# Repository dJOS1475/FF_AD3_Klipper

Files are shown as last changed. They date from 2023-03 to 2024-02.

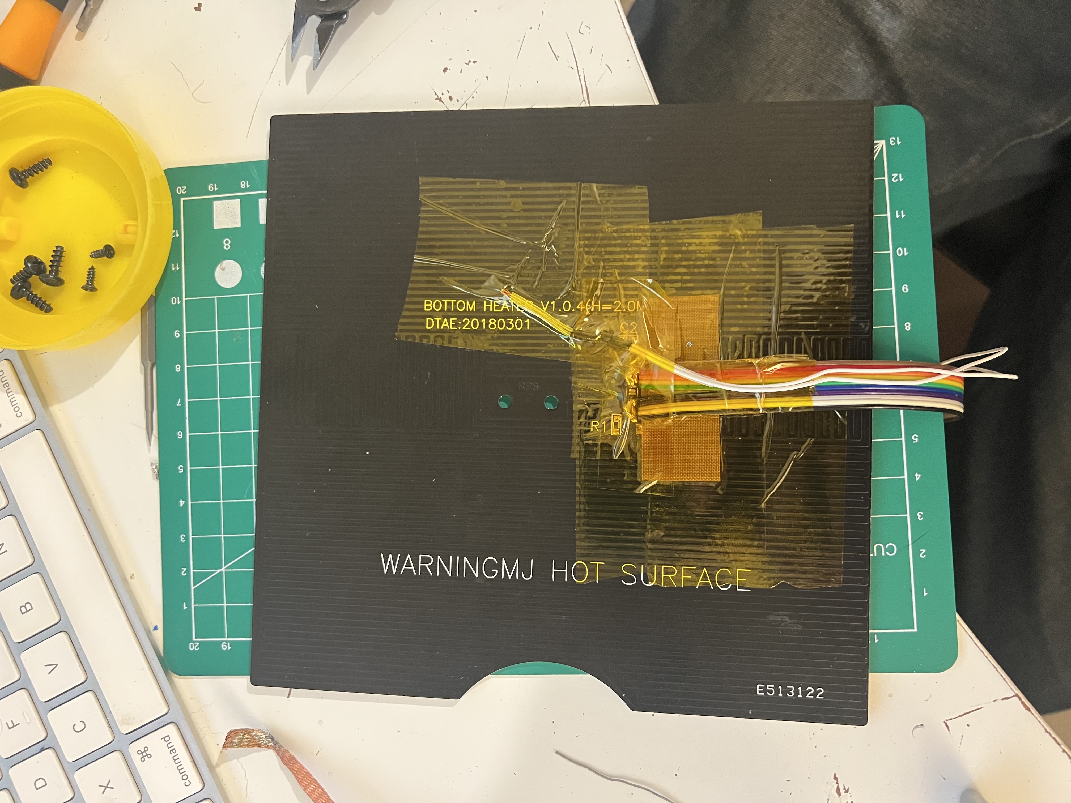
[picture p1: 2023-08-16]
Heater Bed Wiring/IMG_7578.jpeg

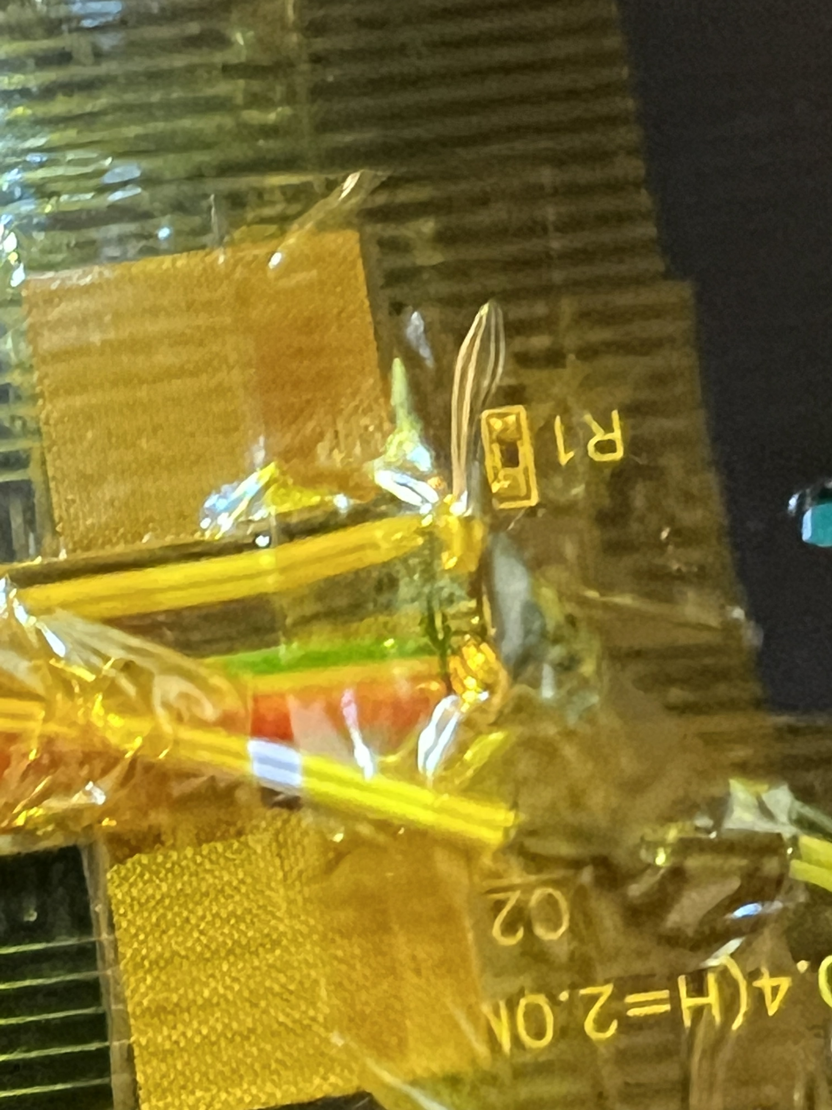
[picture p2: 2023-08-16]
Heater Bed Wiring/IMG_7576.jpeg

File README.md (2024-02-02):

# FlashForge Adventure 3 - Klipper + BTT SKR Mini E3 Upgrade

<p align="center">
  <a>
    Klippventurer logo
  </a>
</p>

Warning: this Upgrade is a Major effort and is recomended for Advanced 3D Printer Users with some electronics skills only. If you would like to keep your OEM mainboard and wiring, please see the Klippventure project by VioSynthax.

# 3D Printed items
are available via Printables:

https://www.printables.com/model/437968-flashforge-adventurer-3-klipper-revo-6-bltouch-btt

# Required Components:
* BigTree Tech SKR Mini E3 v3
* BigTree Tech TFT-35 MZ LCD Screen (with NoTouch E3 Firmware installed)
* PCB's: AD3 HE and AD3 HE BreakOut Boards.
* E3D Revo 6 Hot End
* Good Quality Ribbon cable - ~1.5 meters
* 2x9 Pin IDC Cable Connectors and sockets
* 2x Molex, Micro-Fit 3.0, 43650, 2 Way, 1 Row, Right Angle PCB Headers
* Assorted JST-PH PCB Sockets and Cable Connectors
* 2x PCB Mount Screw Terminal Blocks eg CUI Devices TB004-508-02BE
* 24v to 5v voltage converter eg "1PZ VAC-H15" to power your Raspberry Pi
* Printed Parts

# UPDATES:
* 12th April 2023 - fixed filament macros - please see the Filament_Sensor.cfg file for prerequisites  
* 2nd April 2023 - reduced max speed to 100mm/s - any higher results in layer shifts due to the temps getting too high for the stock stepper motors (at least while printing high tempmaterials like ASA)
* 1st April 2023 - Tweaks to max speed and driver current - the steppers don't seem to like travel speeds over 150mm/s without overheating and causing layer shifts
* 31st March 2023 - Printer now calibrated and Printer.cfg has been updated.
* 30th March 2023 - Everything now works! 

# Videos
FlashForge Adventurer 3 gets a new Brain, Hot-End and Klipper:
https://youtu.be/USZoIhBnA24

Sensorless Homing in Action:
https://youtu.be/0Acrmv7VkdY

and Printing ASA:
https://youtu.be/akCvX6l-e6o

# Klipper Features in use:
* Sensorless Homing
* Adaptive Purge
* Adaptive Mesh Levelling w/ BLTouch
* Auto-Load Filament using Filament Sensor
* Auto Unload Filament when run-out detected
* Unload macro for when you just want to change Filament types/colours etc
* Auto-Extraction Fan at the end of Print (via End G-Code)
* Working LED lighting

# NOTE: 
The factory belt tension on this printer is too loose to exceed 1k acceleration and 100mm/s print speeds. To rectify this you need to retension the X and Y axis belts properly (tight is good, but dont over do it). The Y axis is a PITA as it can only be fixed when the printer is fully disassembled. The Y belt is a continuous loop with no tension adjuster. So you'll need to cut out roughly 5mm from the belt and re-install it as snug as you can get it. I then used some "Selly's Power Grip" to ensure the belts dont jump out of the jaws holding them.

If you still have Y axis layer shifting, I recommend replacing the motor with a better quality unit.

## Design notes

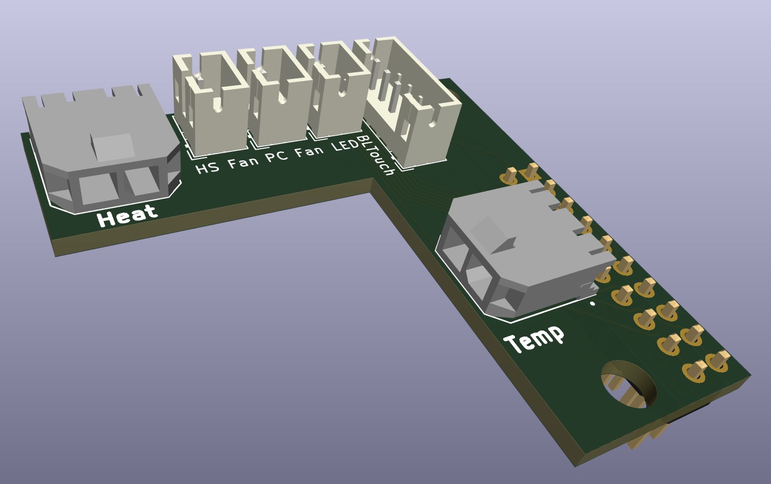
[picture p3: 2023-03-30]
PCB's/Hot End PCB.jpg

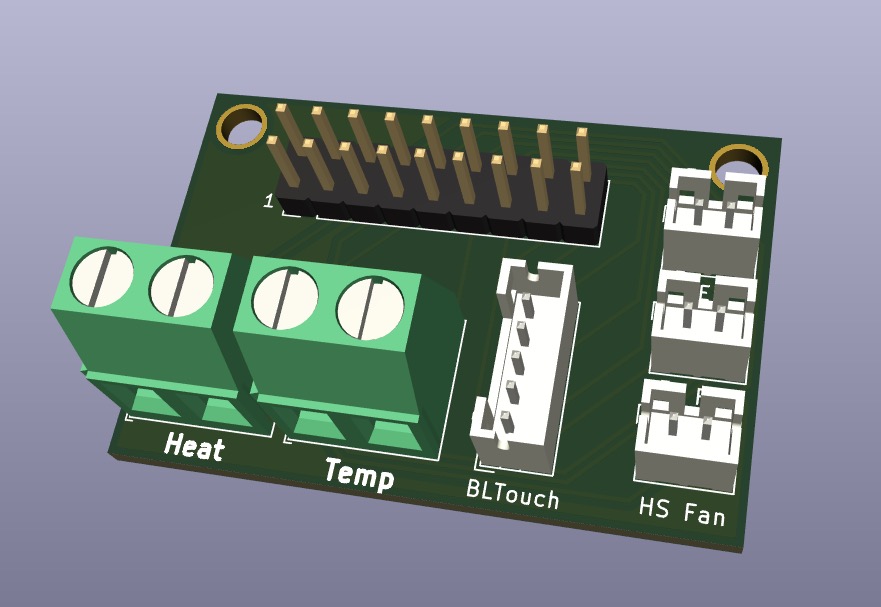
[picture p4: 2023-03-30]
PCB's/Break_Out_Board PCB.jpg

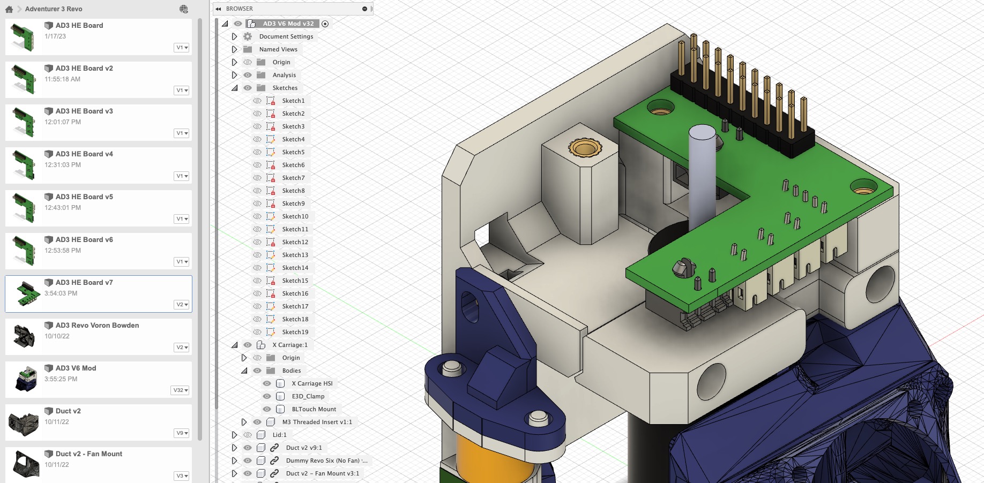
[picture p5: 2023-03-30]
PCB's/Hot End Render.jpg

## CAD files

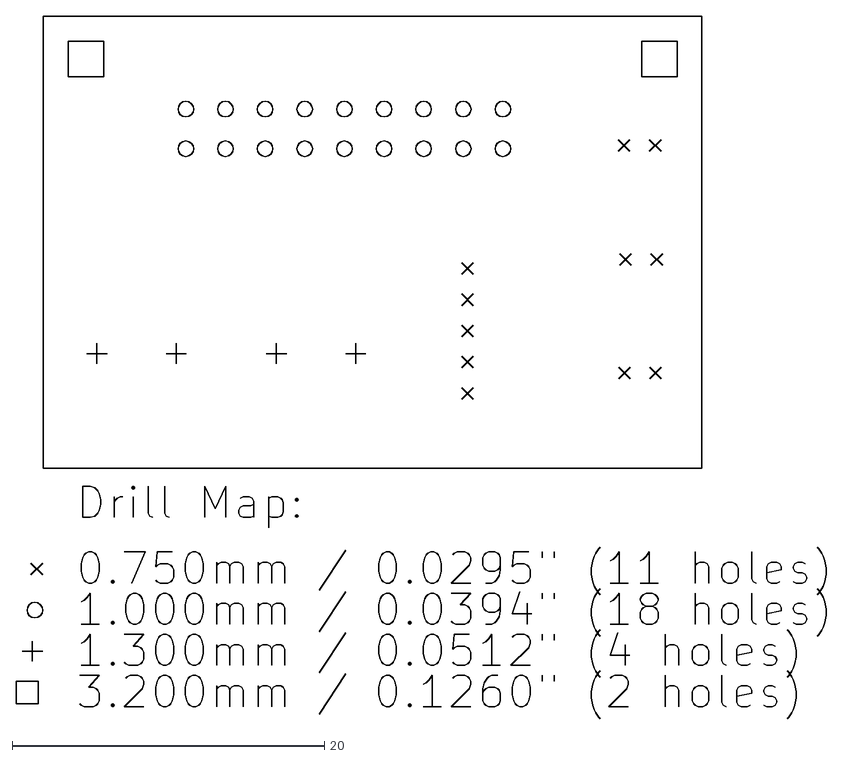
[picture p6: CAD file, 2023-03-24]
PCB's/AD3 Breakout Board/Gerbers/AD3 Breakout Board-drl_map.dxf
51.9 x 45.0

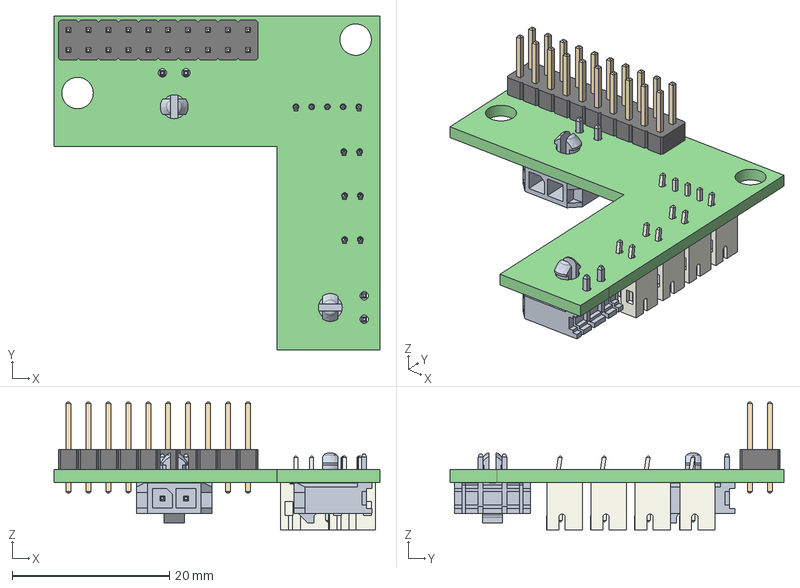
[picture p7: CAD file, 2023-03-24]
PCB's/AD3 HE Board/AD3 HE Board.step
41.5 x 42.5 x 16.2 mm
AD3 HE Board PCB

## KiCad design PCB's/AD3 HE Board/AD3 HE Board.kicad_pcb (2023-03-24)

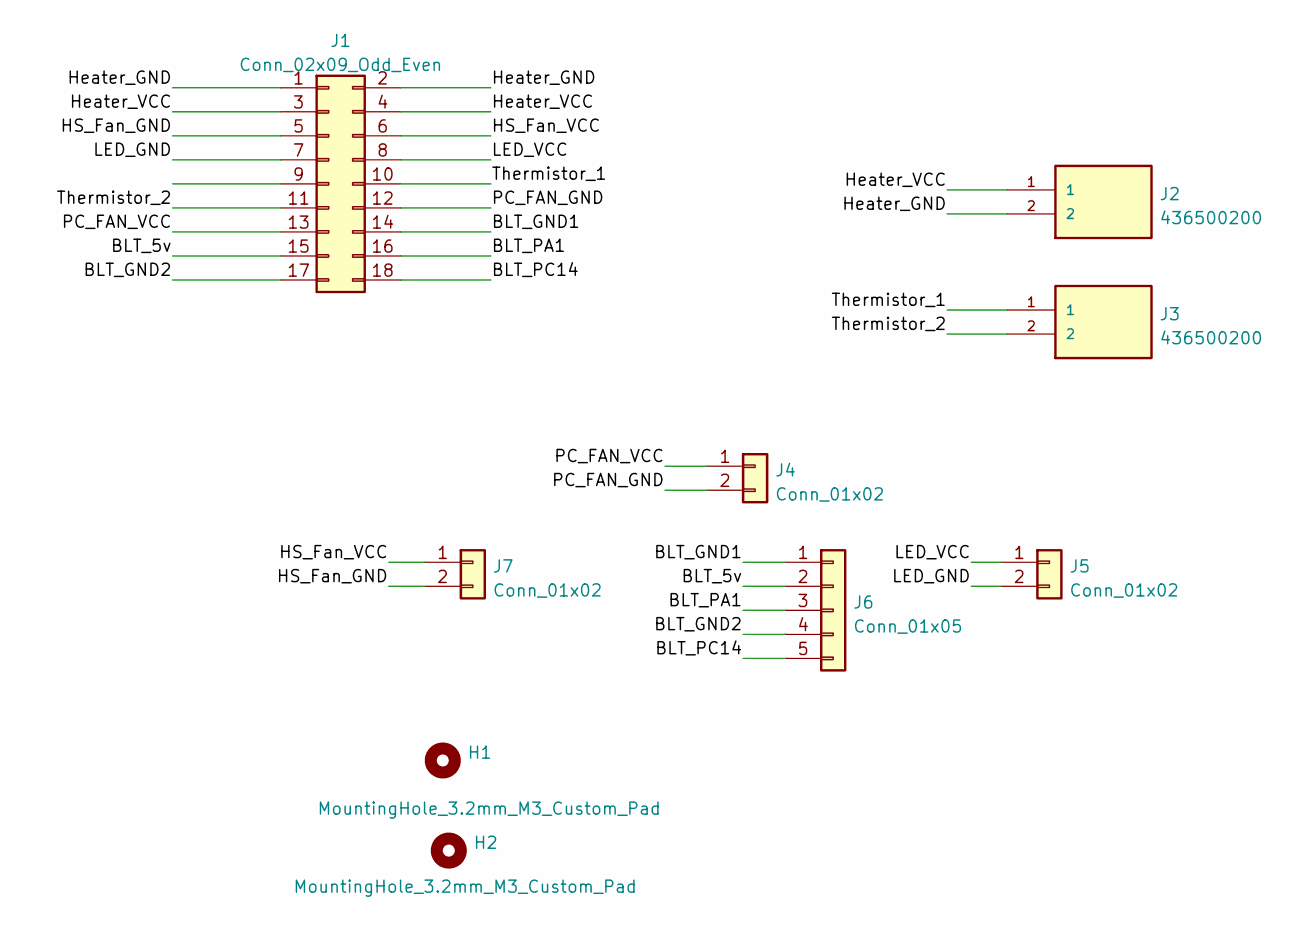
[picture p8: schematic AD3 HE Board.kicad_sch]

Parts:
H1, H2: MountingHole_3.2mm_M3_Custom_Pad
J1: Conn_02x09_Odd_Even; PinHeader_2x09_P2.54mm_Vertical
J2, J3: 436500200; MOLEX_436500200; PARTREV D7
J4, J5, J7: Conn_01x02; JST_PH_B2B-PH-K_1x02_P2.00mm_Vertical
J6: Conn_01x05; JST_PH_B5B-PH-K_1x05_P2.00mm_Vertical

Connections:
/BLT_5v: J1.15, J6.2
/BLT_GND1: J1.14, J6.1
/BLT_GND2: J1.17, J6.4
/BLT_PA1: J1.16, J6.3
/BLT_PC14: J1.18, J6.5
/HS_Fan_GND: J1.5, J7.2
/HS_Fan_VCC: J1.6, J7.1
/Heater_GND: J1.1, J1.2, J2.2
/Heater_VCC: J1.3, J1.4, J2.1
/LED_GND: J1.7, J5.2
/LED_VCC: J1.8, J5.1
/PC_FAN_GND: J1.12, J4.2
/PC_FAN_VCC: J1.13, J4.1
/Thermistor_1: J1.10, J3.1
/Thermistor_2: J1.11, J3.2

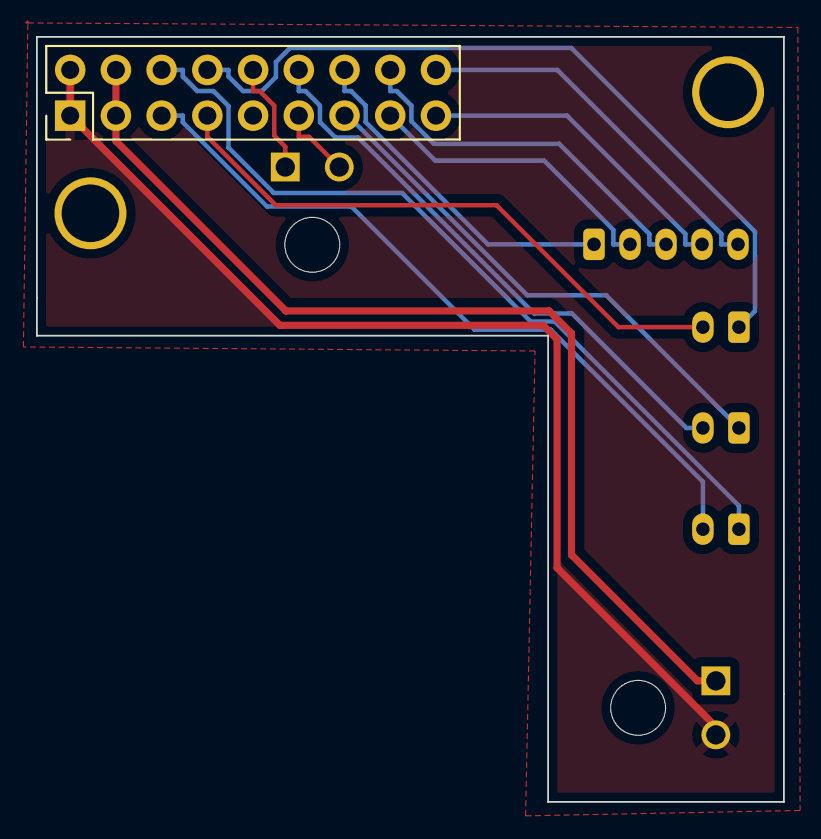
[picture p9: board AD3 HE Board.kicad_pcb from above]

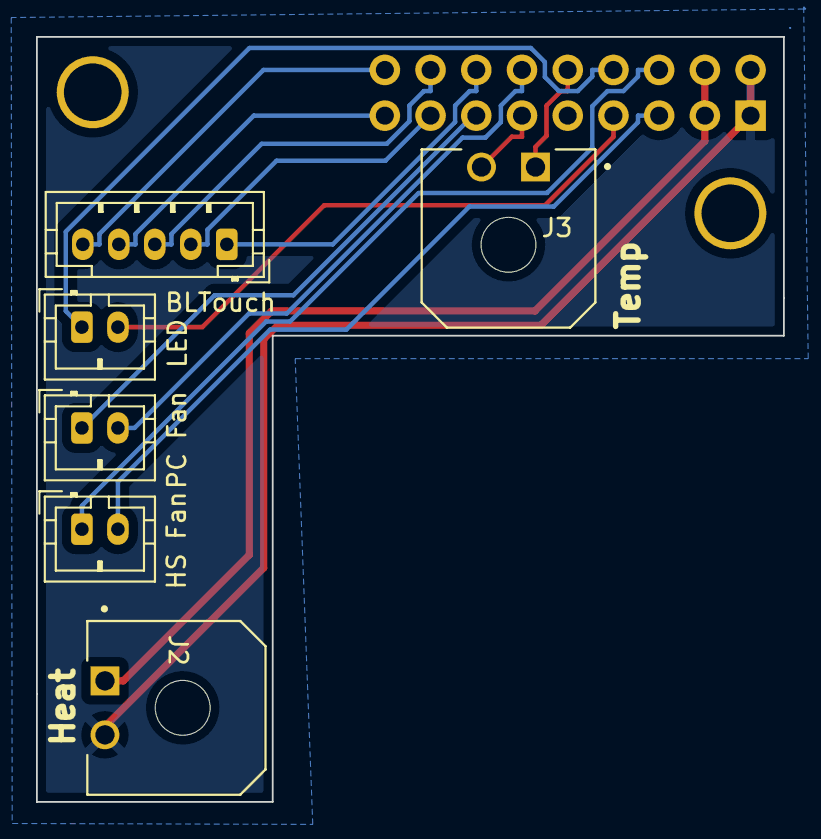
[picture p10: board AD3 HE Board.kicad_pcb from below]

Board: 2 copper layers, 41.5 x 42.5 mm, 9 parts (6 on the bottom side), 15 nets.

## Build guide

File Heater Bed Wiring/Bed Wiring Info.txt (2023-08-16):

Basically you dont want to use the inner 2 traces as that is the old Thermistor. 
I couldnt work out a way to make it reliable, so I replaced it with a normal glass bead thermistor and removed the SMD components from it.

The rest of the pads are split evenly on either side as the heater power. 
It's not important which way you wire it as it isnt polarised.

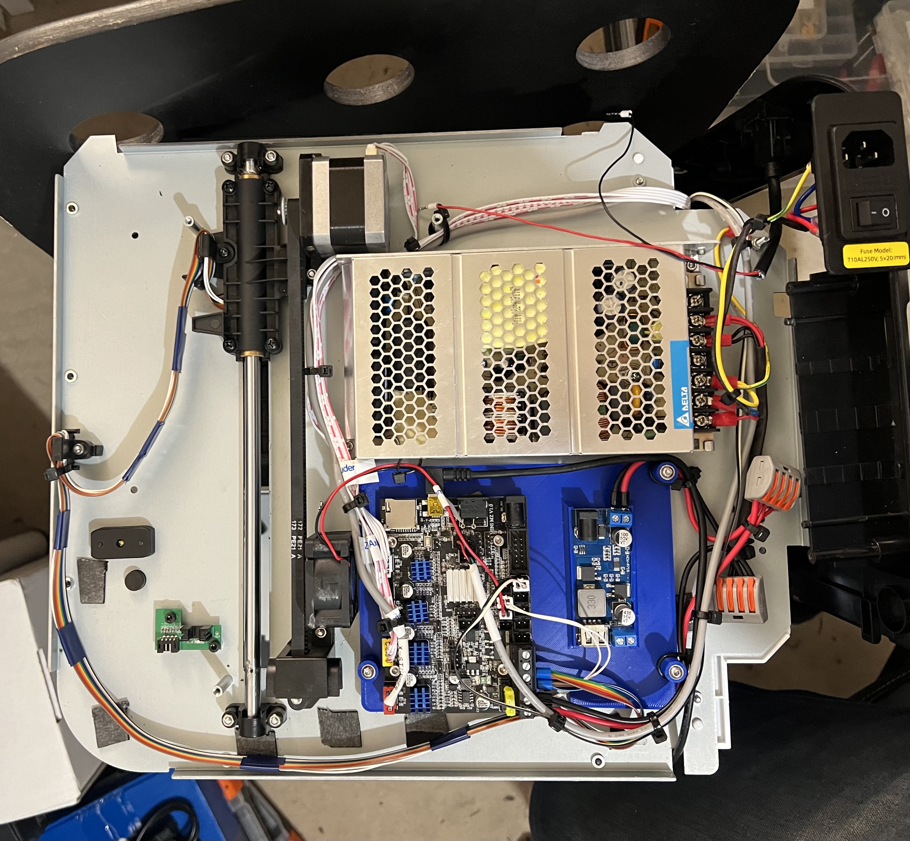
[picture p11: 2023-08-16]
Heater Bed Wiring/IMG_7589.jpeg

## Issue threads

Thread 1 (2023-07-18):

X should be Y

devimauz, 2023-07-18:
https://github.com/dJOS1475/FF_AD3_Klipper/blame/f0657e87483728f9c68891eaef96df8fc055af23/Klipper%20Base%20Config/macros.cfg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

dJOS1475, 2023-07-19:
Could catch, I've fixed it.

dJOS1475, 2023-07-19:
fixed

Closed 2023-07-19.

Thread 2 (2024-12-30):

Different versions of the heated bed

tweinschenk, 2024-12-30:
Hello,

I read the bed wiring info and while looking at my own bed I have to say that the outer two traces are connected to the original thermistor. Maybe we have different versions of the bed? But they even have the same version number: V1.0.4

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

Maybe you can confirm that yours is different and add a note that there are different versions :)

dJOS1475, 2024-12-30:
Howdy, even tho they say they are the same version, your text is in a different orientation to mine. If you rotated your board to the same as shown in my pics, your text would be upside down.

dJOS1475, 2024-12-30:
Ps R1 is a resistor, not the thermistor - it just there as an initial load for the original electronics.

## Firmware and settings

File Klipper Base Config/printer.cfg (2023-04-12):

# This file contains common pin mappings for the BIGTREETECH SKR mini
# E3 v3.0. To use this config, the firmware should be compiled for the
# STM32G0B1 with a "8KiB bootloader" and USB communication.

# The "make flash" command does not work on the SKR mini E3. Instead,
# after running "make", copy the generated "out/klipper.bin" file to a
# file named "firmware.bin" on an SD card and then restart the SKR
# mini E3 with that SD card.

# See docs/Config_Reference.md for a description of parameters.

[include Adaptive_Mesh.cfg]
[include Adaptive_Purge.cfg]
[include macros.cfg] 
[include probe_bltouch.cfg]
[include mainsail.cfg]
[include Filament_Sensor.cfg]

[printer]
kinematics: cartesian
max_velocity: 150
max_accel: 3000
max_accel_to_decel: 3000
max_z_accel: 25
square_corner_velocity: 5

[stepper_x]
step_pin: PB13
dir_pin: PB12
enable_pin: !PB14
microsteps: 16
rotation_distance: 33.36
endstop_pin: tmc2209_stepper_x:virtual_endstop
homing_retract_dist: 0
homing_speed: 25
position_endstop: 0
position_max: 156


[tmc2209 stepper_x]
uart_pin: PC11
tx_pin: PC10
uart_address: 0
run_current: 0.800
stealthchop_threshold: 999999
diag_pin: ^PC0      # Set to MCU pin connected to TMC DIAG pin
driver_SGTHRS: 75  # 255 is most sensitive value, 0 is least sensitive


[stepper_y]
step_pin: PB10
dir_pin: PB2
enable_pin: !PB11
microsteps: 16
rotation_distance: 33.38
endstop_pin: tmc2209_stepper_y:virtual_endstop
homing_retract_dist: 0
homing_speed: 25
position_endstop: 0
position_max: 148


[tmc2209 stepper_y]
uart_pin: PC11
tx_pin: PC10
uart_address: 2
run_current: 0.800
stealthchop_threshold: 999999
diag_pin: ^PC1      # Set to MCU pin connected to TMC DIAG pin
driver_SGTHRS: 75  # 255 is most sensitive value, 0 is least sensitive


[stepper_z]
step_pin: PB0
dir_pin: PC5
enable_pin: !PB1
microsteps: 16
rotation_distance: 6.25
# endstop_pin: PC2
endstop_pin: probe:z_virtual_endstop
# position_endstop: 0
position_max: 150
homing_speed: 20
second_homing_speed: 15
homing_retract_dist: 5

[tmc2209 stepper_z]
uart_pin: PC11
tx_pin: PC10
uart_address: 1
run_current: 0.800
stealthchop_threshold: 999999


[extruder]
step_pin: PB3
dir_pin: !PB4
enable_pin: !PD1
microsteps: 16
rotation_distance: 31
nozzle_diameter: 0.4
filament_diameter: 1.750
heater_pin: PC8
sensor_type: ATC Semitec 104NT-4-R025H42G 
sensor_pin: PC4
min_temp: 0
max_temp: 300
min_extrude_temp: 180
max_extrude_only_distance: 900
max_extrude_only_velocity: 120
max_extrude_only_accel: 1000
min_extrude_temp: 180
max_extrude_cross_section: 5
pressure_advance: 0.050
# pressure_advance_smooth_time: 0.04

[tmc2209 extruder]
uart_pin: PC11
tx_pin: PC10
interpolate: True
uart_address: 3
run_current: 1.3
stealthchop_threshold: 0


[heater_bed]
heater_pin: PC9
sensor_type: Generic 3950
sensor_pin: PA0
min_temp: 0
max_temp: 120


[idle_timeout]
gcode:
  PANEL_BEEP   
  M84 ; disable motors
  TURN_OFF_HEATERS
  SET_PIN PIN=led_lights VALUE=0.00
  M117 Ready
timeout: 3600

[bltouch]
x_offset: -13.25
y_offset: 10.0
#z_offset: 5.0

[heater_fan hotend_fan]
#Heatbreak Cooling Fan
pin: PC6
heater: extruder
heater_temp: 50.0

[fan_generic exhaust_fan]
#Chamber Cooling Fan
pin: PB15


[fan]
#Part Cooling Fan
pin: PC7

[mcu]
serial: /dev/serial/by-id/usb-Klipper_stm32g0b1xx_5200320007504B5735313920-if00

[mcu rpi]
serial: /tmp/klipper_host_mcu


[output_pin led_lights]
pin: PA8
value: 1

[gcode_arcs]
resolution: 1.0

[force_move]
enable_force_move: True
#   Set to true to enable FORCE_MOVE and SET_KINEMATIC_POSITION
#   extended G-Code commands. The default is false.

[exclude_object]

[skew_correction]

[display_status]

[pause_resume]

[display]
lcd_type: emulated_st7920
en_pin: EXP1_7
spi_software_sclk_pin: EXP1_6
spi_software_mosi_pin: EXP1_8
spi_software_miso_pin: PA3
encoder_pins: ^EXP1_5, ^EXP1_3
click_pin: ^!EXP1_2

[temperature_sensor raspberry_pi]
sensor_type: temperature_host
min_temp: 10
max_temp: 100


[temperature_sensor mcu_temp]
sensor_type: temperature_mcu
min_temp: 0
max_temp: 100

[output_pin BEEPER_pin]
pin: EXP1_1
#   Beeper pin. This parameter must be provided.
pwm: True
#   A piezo beeper needs a PWM signal, a DC buzzer doesn't.
value: 0
#   Silent at power on, set to 1 if active low.
shutdown_value: 0
#   Disable at emergency shutdown (no PWM would be available anyway).
cycle_time: 0.001
#   Default PWM frequency : 0.001 = 1ms will give a tone of 1kHz
#   Although not pitch perfect.

[respond]
default_type: echo
#   Sets the default prefix of the "M118" and "RESPOND" output to one
#   of the following:
#       echo: "echo: " (This is the default)
#       command: "// "
#       error: "!! "
default_prefix: echo:
#   Directly sets the default prefix. If present, this value will
#   override the "default_type".

[menu __main __octoprint]
type: disabled

[board_pins]
aliases:
    # EXP1 header
    EXP1_1=PB5,  EXP1_3=PA9,   EXP1_5=PA10, EXP1_7=PB8, EXP1_9=<GND>,
    EXP1_2=PA15, EXP1_4=<RST>, EXP1_6=PB9,  EXP1_8=PD6, EXP1_10=<5V>

# See the sample-lcd.cfg file for definitions of common LCD displays.

#*# <---------------------- SAVE_CONFIG ---------------------->
#*# DO NOT EDIT THIS BLOCK OR BELOW. The contents are auto-generated.
#*#
#*# [extruder]
#*# control = pid
#*# pid_kp = 35.959
#*# pid_ki = 4.795
#*# pid_kd = 67.424
#*#
#*# [heater_bed]
#*# control = pid
#*# pid_kp = 61.177
#*# pid_ki = 0.917
#*# pid_kd = 1020.890
#*#
#*# [bed_mesh default]
#*# version = 1
#*# points =
#*# 	  -0.302734, 0.066406, 0.224609, 0.111328
#*# 	  -0.265625, -0.039062, 0.021484, -0.023438
#*# 	  -0.283203, -0.080078, -0.031250, -0.101562
#*# tension = 0.2
#*# min_x = 21.03
#*# algo = lagrange
#*# y_count = 3
#*# mesh_y_pps = 2
#*# min_y = 39.519999999999996
#*# x_count = 4
#*# max_y = 108.46
#*# mesh_x_pps = 2
#*# max_x = 128.97
#*#
#*# [bltouch]
#*# z_offset = 2.443
#*#
#*# [skew_correction my_skew_profile]
#*# xy_skew = -0.0008904302644857634
#*# xz_skew = 0.0
#*# yz_skew = 0.0

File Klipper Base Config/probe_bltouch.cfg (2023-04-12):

#bltouch.cfg

[bltouch]
sensor_pin: PC14
control_pin: PA1
probe_with_touch_mode: True
# Offsets in printer.cfg
speed: 5.0
lift_speed: 10.00
samples: 3
samples_result: median
sample_retract_dist: 3.0
samples_tolerance: 0.05
samples_tolerance_retries: 2
pin_move_time: 0.680
stow_on_each_sample: False
probe_with_touch_mode: True
pin_up_reports_not_triggered: True
pin_up_touch_mode_reports_triggered: True

#[safe_z_home]
#home_xy_position: 110,67
#speed: 25.0
#z_hop: 10
#z_hop_speed: 10.0
#move_to_previous: False

[homing_override]
set_position_z: 5
gcode:
    G1 Z+25 F1000
    HOME_X
    HOME_Y
    #Home Z
    G1 X110 Y67 F1500
    G28 Z
    G1 Z+25 F1000

[bed_mesh]
speed: 100
horizontal_move_z: 10
mesh_min: 19.75, 10
mesh_max: 142.75, 150
probe_count: 4,4
fade_start: 1.0
fade_end: 10
mesh_pps: 2,2
fade_target: 0
#algorithm: bicubic
#bicubic_tension: 0.2
#move_check_distance: 5
#split_delta_z: .025

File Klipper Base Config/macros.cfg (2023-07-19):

#macros.cfg

[gcode_macro G29]
gcode:
    BED_MESH_CALIBRATE

[gcode_macro HOME_X]
gcode:
    {% set HOME_CUR = 0.500 %}
    {% set driver_config = printer.configfile.settings['tmc2209 stepper_x'] %}
    {% set RUN_CUR = driver_config.run_current %}
    # Set current for sensorless homing
    SET_TMC_CURRENT STEPPER=stepper_x CURRENT={HOME_CUR}
    # Pause to ensure driver stall flag is clear
    G4 P2000
    # Home
    G28 X0
    # Move away
    G1 X5 F1500
    # Set current during print
    SET_TMC_CURRENT STEPPER=stepper_x CURRENT={RUN_CUR}

[gcode_macro HOME_Y]
gcode:
    {% set HOME_CUR = 0.500 %}
    {% set driver_config = printer.configfile.settings['tmc2209 stepper_y'] %}
    {% set RUN_CUR = driver_config.run_current %}
    # Set current for sensorless homing
    SET_TMC_CURRENT STEPPER=stepper_x CURRENT={HOME_CUR}
    # Pause to ensure driver stall flag is clear
    G4 P2000
    # Move away
    G28 Y0
    # Move away
    G1 y5 F1500
    # Set current during print
    SET_TMC_CURRENT STEPPER=stepper_y CURRENT={RUN_CUR}


[gcode_macro M300]
gcode:
    # Use a default 1kHz tone if S is omitted.
    {% set S = params.S|default(1000)|int %}
    # Use a 10ms duration is P is omitted.
    {% set P = params.P|default(100)|int %}
    SET_PIN PIN=BEEPER_pin VALUE=0.5 CYCLE_TIME={ 1.0/S if S > 0 else 1 }
    G4 P{P}
    SET_PIN PIN=BEEPER_pin VALUE=0



[gcode_macro PANEL_BEEP]
gcode:
    # Use a default 1kHz tone if S is omitted.
    {% set S = params.S|default(1000)|int %}
    # Use a 10ms duration is P is omitted.
    {% set P = params.P|default(100)|int %}
    SET_PIN PIN=BEEPER_pin VALUE=0.5 CYCLE_TIME={ 1.0/S if S > 0 else 1 }
    G4 P{P}
    SET_PIN PIN=BEEPER_pin VALUE=0


[gcode_macro M600]
gcode:
    {% set X = params.X|default(1)|float %}
    {% set Y = params.Y|default(1)|float %}
    {% set Z = params.Z|default(145)|float %}
    SAVE_GCODE_STATE NAME=M600_state
    PAUSE
    G91
    #G1 E-.8 F2700
    G1 Z{Z}
    G90
    G1 X{X} Y{Y} F3000
    G91
    G1 E-50 F1000
    RESTORE_GCODE_STATE NAME=M600_state


[gcode_macro Load_Filament]
gcode:
    G28 ; Home Axis
    G21 ;Let the printer know you are following this point with metric values
    G90 ;Let the printer know you are using absolute positioning
    G28 X Y ;move extruder back to front left corner
    G1 X15 Z15.0 ;move the Z axis 15mm
    FILAMENT_LOAD


[gcode_macro Unload_Filament]
gcode:
    G28 ; Home Axis
    G21 ;Let the printer know you are following this point with metric values
    G90 ;Let the printer know you are using absolute positioning
    G28 X Y ;move extruder back to front left corner
    G1 X15 Z15.0 ;move the Z axis 15mm
    FILAMENT_UNLOAD


[gcode_macro PAUSE]
description: Pause the actual running print
rename_existing: PAUSE_BASE
gcode:
    PANEL_BEEP
    ##### set defaults #####
    {% set x = params.X|default(1) %}      #edit to your park position
    {% set y = params.Y|default(1) %}      #edit to your park position
    {% set z = params.Z|default(148)|float %} #edit to your park position
    {% set e = params.E|default(2) %}        #edit to your retract length
    ##### calculate save lift position #####
    {% set max_z = printer.toolhead.axis_maximum.z|float %}
    {% set act_z = printer.toolhead.position.z|float %}
    {% set lift_z = z|abs %}
    {% if act_z < (max_z - lift_z) %}
        {% set z_safe = lift_z %}
    {% else %}
        {% set z_safe = max_z - act_z %}
    {% endif %}
    ##### end of definitions #####
    PAUSE_BASE
    G90
    {% if printer.extruder.can_extrude|lower == 'true' %}
      G1 E-{e} F2100
    {% else %}
      {action_respond_info("Extruder not hot enough")}
    {% endif %}
    {% if "xyz" in printer.toolhead.homed_axes %}    
      G1 Z{z_safe}
      G90
      G1 X{x} Y{y} F6000
    {% else %}
      {action_respond_info("Printer not homed")}
    {% endif %}

[gcode_macro RESUME]
description: Resume the actual running print
rename_existing: RESUME_BASE
gcode:
    PANEL_BEEP
    ##### set defaults #####
    {% set e = params.E|default(1) %} #edit to your retract length
    #### get VELOCITY parameter if specified ####
    {% if 'VELOCITY' in params|upper %}
      {% set get_params = ('VELOCITY=' + params.VELOCITY)  %}
    {%else %}
      {% set get_params = "" %}
    {% endif %}
    ##### end of definitions #####
    G91
    {% if printer.extruder.can_extrude|lower == 'true' %}
      G1 E{e} F2100
    {% else %}
      {action_respond_info("Extruder not hot enough")}
    {% endif %}  
    RESUME_BASE {get_params}

[gcode_macro CANCEL_PRINT]
description: Cancel the actual running print
rename_existing: CANCEL_PRINT_BASE
gcode:
    PANEL_BEEP    
    CANCEL_PRINT_BASE    
    G91 ;relative positioning
	G1 E-5 F300 ;retract the filament a bit before lifting the nozzle, to release some of the pressure
	G1 Z+15.0 E-5 ;X-20 Y-20 F{speed_travel} ;move Z up a bit and retract filament even more
	G0 X1 Y1
    SET_SKEW CLEAR=1
	G90 ;Absolute positioning
	G1 Y140 F3000 ;Present print
    TURN_OFF_HEATERS
    CLEAR_PAUSE
    M84 ;steppers off
    M107 ; Fan off
    M117 Cooling down...
    SET_FAN_SPEED FAN=exhaust_fan SPEED=1
    G4 P300000 ; Run exhaust fan for 5 mins
    SET_FAN_SPEED FAN=exhaust_fan SPEED=0
    SET_SKEW CLEAR=1
    M117 Cancelled ...


[gcode_macro ABORT_PRINT]
gcode:
    CANCEL_PRINT


[gcode_macro Calibrate_Pressure_Advance]
gcode:
    SET_VELOCITY_LIMIT SQUARE_CORNER_VELOCITY=1 ACCEL=500
    TUNING_TOWER COMMAND=SET_PRESSURE_ADVANCE PARAMETER=ADVANCE START=0 FACTOR=.020

[gcode_macro Calibrate_Z_Offset]
gcode:
    PROBE_CALIBRATE


[gcode_macro Steppers_Off]
gcode:
    PANEL_BEEP   
    M84 ; disable motors
    M117 Steppers Off.


[gcode_macro PRESENT_PRINT]
gcode:
    M107 ; Fan off
    G91 ;relative positioning
    G1 Z+15.0 ;X-20 Y-20 F{speed_travel} ;move Z up a bit
    G1 X1 Y1 Z15.0 ;move the Z axis 15mm 
    SET_SKEW CLEAR=1
    G90 ;Absolute positioning
    G1 Y140 F3000 ;Present print
    PANEL_BEEP   
    M117 Finished ...


[gcode_macro Excercise_Y]
gcode:
    G1 Z20.0 
    M400
    G1 Y140 F90000
    G1 Y10 F90000
    G1 Y140 F90000
    G1 Y10 F90000
    G1 Y140 F90000
    G1 Y10 F90000
    G1 Y140 F90000
    G1 Y10 F90000    
    G1 Y140 F90000
    G1 Y10 F90000
    G1 Y140 F90000
    G1 Y10 F90000
    G1 Y140 F90000
    G1 Y10 F90000

[gcode_macro Excercise_X]
gcode:
    G1 Z20.0 
    M400
    G1 X150 F90000
    G1 X10 F90000
    G1 X150 F90000
    G1 X10 F90000
    G1 X150 F90000
    G1 X10 F90000
    G1 X150 F90000
    G1 X10 F90000
    G1 X150 F90000
    G1 X10 F90000
    G1 X150 F90000
    G1 X10 F90000
    G1 X150 F90000
    G1 X10 F90000

[gcode_macro Excercise_Z]
gcode:
    G1 X80.0 
    M400
    G1 Z140 F1000
    G1 Z10 F1000
    G1 Z140 F1000
    G1 Z10 F1000
    G1 Z140 F1000
    G1 Z10 F1000
    G1 Z140 F1000
    G1 Z10 F1000
    G1 Z140 F1000
    G1 Z10 F1000
    G1 Z140 F1000
    G1 Z10 F1000
    G1 Z140 F1000
    G1 Z10 F1000

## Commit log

2023-03-24 Add files via upload
    HE BreakOut Board
    [AD3 Breakout Board-B_Cu.gbr, AD3 Breakout Board-B_Mask.gbr, AD3 Breakout Board-B_Paste.gbr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]
2023-03-24 Add files via upload
    HE Board
    [AD3 HE Board-B_Cu.gbr, AD3 HE Board-B_Mask.gbr, AD3 HE Board-B_Paste.gbr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]
2023-03-24 Add files via upload
    Klipper Base Config
    [Adaptive_Mesh.cfg, Adaptive_Purge.cfg, Filament_Sensor.cfg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]
2023-03-24 Add files via upload
    Update Printer.cfg with stepper tweaks
    [printer.cfg]
2023-03-24 Update printer.cfg
    tweaked sensorless homing
    [printer.cfg]
2023-03-30 Add files via upload
    Sensorless Homing now Works
    [macros.cfg, printer.cfg, probe_bltouch.cfg]
2023-04-02 Update printer.cfg
    Updated Speed limits
    [printer.cfg]
2023-04-12 Add files via upload
    Updates
    [Filament_Sensor.cfg, macros.cfg, printer.cfg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]
2023-07-19 Update macros.cfg
    fixed homing config for stepper current in Y axis
    [macros.cfg]
2023-08-16 Create Bed Wiring Info.txt
2023-08-16 Update Bed Wiring Info.txt
